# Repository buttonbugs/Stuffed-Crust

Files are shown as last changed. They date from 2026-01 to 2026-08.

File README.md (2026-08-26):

# Stuffed Crust



This repository contains the code for Wildcat Robotics' team Stuffed Crust. This is a fork of the open source melty brain code, openmelt [^1], with improved translational drift algorithm, adapted watchdog [^2] for [Teensy 4.0](https://www.pjrc.com/store/teensy40.html) and some other changes specific to Stuffed Crust's design.

## Preview

https://github.com/user-attachments/assets/2b465f3a-5d59-4c2d-9435-344acd4d646b

### References

[^1]: R. Olson and M. Schoppert, [“nothinglabs/openmelt2,”](https://github.com/nothinglabs/openmelt2/) July 2026. original-date: 2023-03-04T03:05:36Z.

[^2]: A. Brewer and S. Nobs, [“tonton81/WDT t4,”](https://github.com/tonton81/WDT_T4) Feb. 2026. original-date: 2020-01-
26T16:30:28Z.

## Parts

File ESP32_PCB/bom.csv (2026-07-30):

Qty | Comment | DNP | Exclude from BOM | Exclude from Board | Designator | Footprint | LCSC PN | Datasheet
3 | 1uF |  |  |  | C1,C2,C4 | Capacitor_SMD:C_0603_1608Metric | C15849 | ~
1 | 6.8uF |  |  |  | C3 | Capacitor_Tantalum_SMD:CP_EIA-3216-18_Kemet-A | C444749 | ~
1 | 10uF |  |  |  | C5 | Capacitor_Tantalum_SMD:CP_EIA-3216-18_Kemet-A | C7171 | ~
3 | 100nF |  |  |  | C6,C8,C13 | Capacitor_SMD:C_0603_1608Metric | C14663 | ~
1 | 10pF |  |  |  | C7 | Capacitor_SMD:C_0603_1608Metric | C106245 | ~
1 | 82pF |  |  |  | C9 | Capacitor_SMD:C_0603_1608Metric | C1683
1 | 47uF |  |  |  | C10 | Capacitor_SMD:C_0805_2012Metric | C16780
1 | 22uF |  |  |  | C11 | Capacitor_SMD:C_0603_1608Metric | C86295
1 | BAT54CW |  |  |  | D1 | Package_TO_SOT_SMD:SOT-323_SC-70 | C192144 | https://assets.nexperia.com/documents/data-sheet/BAT54W_SER.pdf
2 | SMAJ36A |  |  |  | D2,D3 | Diode_SMD:D_SMA | C148232 | https://www.littelfuse.com/media?itemid=75e32973-b177-4ee3-a0ff-cedaf1abdb93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
1 | Status_LED |  |  |  | D4 | LED_SMD:LED_0603_1608Metric | C19273151 | ~
1 | Power_LED |  |  |  | D5 | LED_SMD:LED_0603_1608Metric | C19171390 | ~
1 | USB_C_Receptacle |  |  |  | J1 | Connector_USB:USB_C_Receptacle_Molex_105450-0101 | C134092 | https://www.usb.org/sites/default/files/documents/usb_type-c.zip
1 | ESC 1 |  |  |  | J2 | ESC_Connectors:3_Pin |  | ~
1 | ESC 2 |  |  |  | J3 | ESC_Connectors:3_Pin |  | ~
1 | EN & Boot |  |  |  | J4 | Connector_PinHeader_2.54mm:PinHeader_2x04_P2.54mm_Vertical | C32713277 | ~
1 | LED_Strip |  |  |  | J5 | ESC_Connectors:LED_Strip |  | ~
1 | 10uH |  |  |  | L1 | Inductor_SMD:L_APV_APH0630 | C5349698 | ~
1 | 5.1K |  |  |  | R1 | Resistor_SMD:R_0603_1608Metric | C2907044 | ~
1 | 5.1k |  |  |  | R2 | Resistor_SMD:R_0603_1608Metric | C2907044 | ~
2 | 4.7k |  |  |  | R3,R4 | Resistor_SMD:R_0603_1608Metric | C99782 | ~
4 | 10k |  |  |  | R5,R6,R9,R12 | Resistor_SMD:R_0603_1608Metric | C98220 | ~
1 | 100k |  |  |  | R7 | Resistor_SMD:R_0805_2012Metric | C7319379 | ~
1 | 13.7 |  |  |  | R8 | Resistor_SMD:R_0805_2012Metric | C409962 | ~
2 | 100Ω |  |  |  | R10,R11 | Resistor_SMD:R_0603_1608Metric | C105588 | ~
1 | H3LIS331DL |  |  |  | U2 | accelerometer:TFLGA16_3X3X1_STM | C2655074 | https://www.st.com/resource/en/datasheet/h3lis331dl.pdf
1 | AP2112K-3.3 |  |  |  | U3 | Package_TO_SOT_SMD:SOT-23-5 | C23380830 | https://www.diodes.com/assets/Datasheets/AP2112.pdf
1 | TPS54302 |  |  |  | U4 | Package_TO_SOT_SMD:SOT-563 | C50310967 | http://www.ti.com/lit/ds/symlink/tps54302.pdf
1 | ESP32-S3-MINI-1U |  |  |  | U5 | RF_Module:ESP32-S2-MINI-1U | C2980299 | https://www.espressif.com/sites/default/files/documentation/esp32-s3-mini-1_mini-1u_datasheet_en.pdf

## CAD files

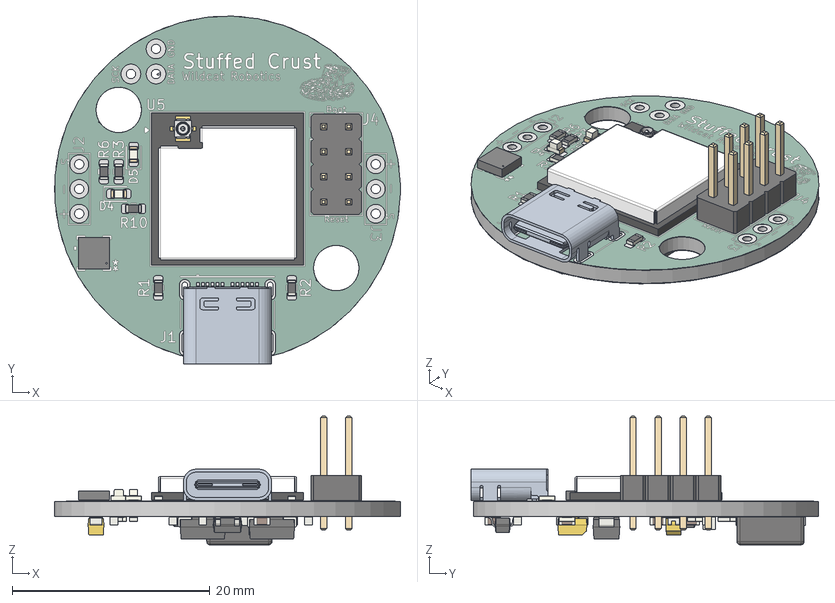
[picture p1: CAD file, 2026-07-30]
ESP32_PCB/ESP32_PCB.step
35.0 x 35.2 x 13.0 mm
R_0603_1608Metric x 10
LED_0603_1608Metric x 2
H3LIS331DLTR
PinHeader_2x04_P2.54mm_Vertical
uid__2482
C0402_20210301.xtd
C0201_20210301.xtd x 13
R0201_20210301.xtd x 3
ESP32-S3_20210301.xtd
ipx3.xtd
DFN1006.xtd
L0201_20210301.xtd x 2
XTAL3225_20210301.xtd
Imported
ESP32-S3-S2-MINI-solder_pad
ShieldBox_ESP32-S2-MINI-1U_V1.1_20231124
SOT-323_SC-70
D_SMA x 2
C_0603_1608Metric x 9
R_0805_2012Metric x 2
C_0805_2012Metric
CP_EIA-3216-18_Kemet-A x 2
L_APV_APH0630
TSOT-23-6
SOT-23-5
ESP32_PCB_copper
ESP32_PCB_pad
ESP32_PCB_via
ESP32_PCB_silkscreen x 2
ESP32_PCB_soldermask x 2
ESP32_PCB_PCB

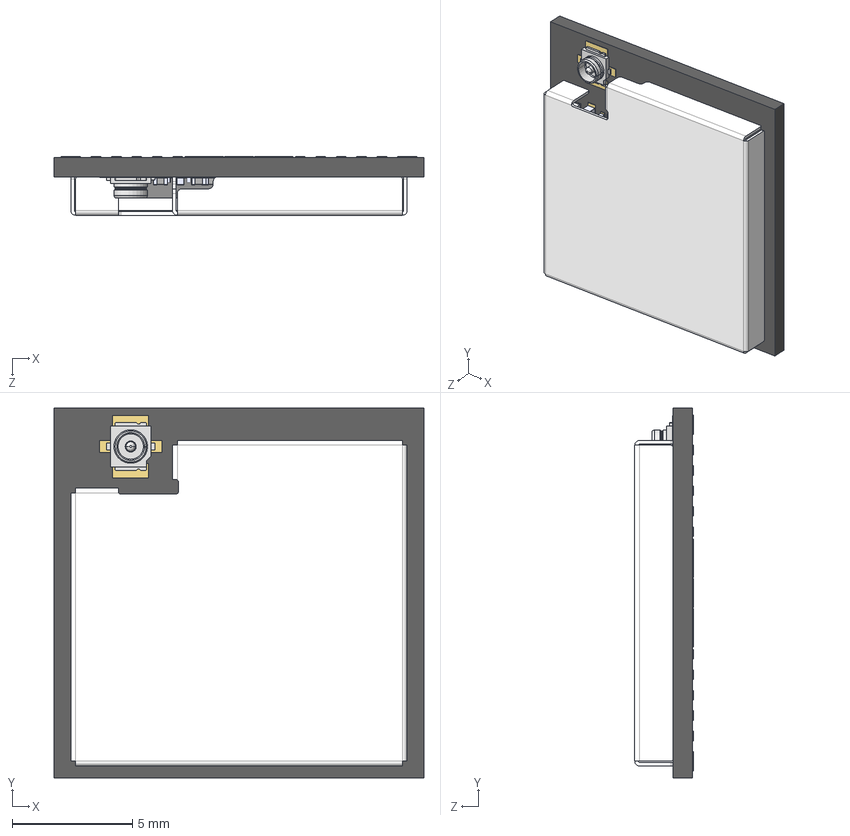
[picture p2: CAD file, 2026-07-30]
ESP32_PCB/imports/ESP32-S3-MINI-1U/ESP32-S3-MINI-1U.STEP
15.4 x 15.4 x 2.44 mm
uid__2482
C0402_20210301.xtd
C0201_20210301.xtd x 13
R0201_20210301.xtd x 3
ESP32-S3_20210301.xtd
ipx3.xtd
DFN1006.xtd
L0201_20210301.xtd x 2
XTAL3225_20210301.xtd
Imported
ESP32-S3-S2-MINI-solder_pad
ShieldBox_ESP32-S2-MINI-1U_V1.1_20231124

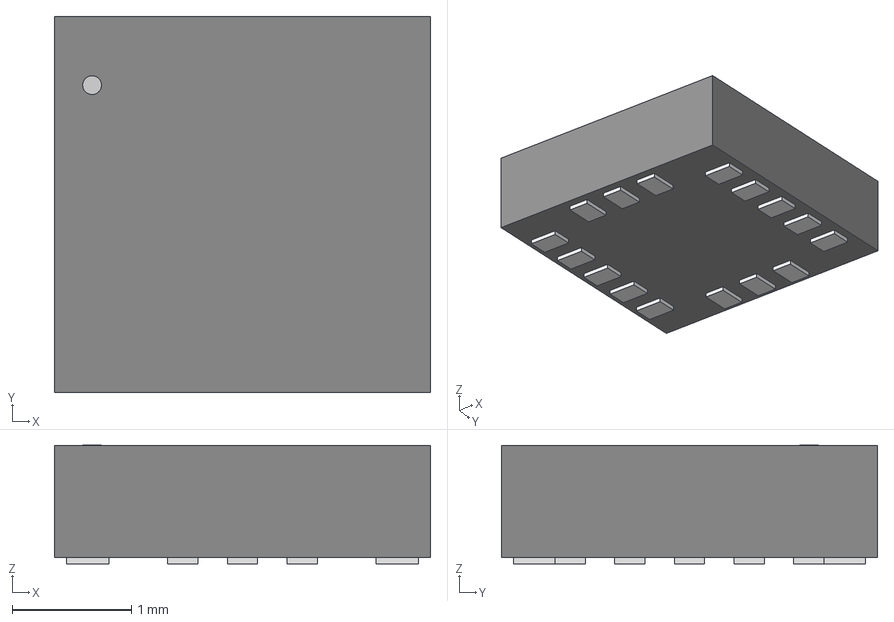
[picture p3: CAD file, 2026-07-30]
ESP32_PCB/imports/ul_H3LIS331DL/H3LIS331DLTR.step
3.15 x 3.15 x 0.993 mm

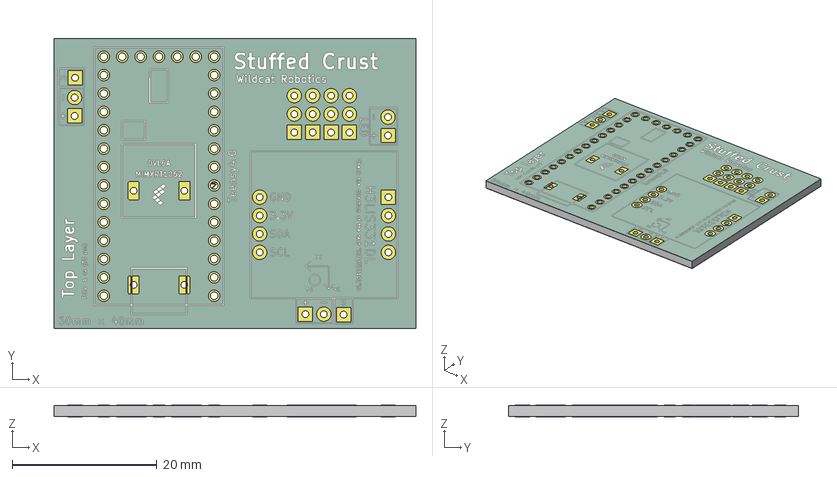
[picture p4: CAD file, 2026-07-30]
PCB/3D_models/PCB_v1.step
50.0 x 40.0 x 1.66 mm
PCB_v1_copper
PCB_v1_silkscreen x 2
PCB_v1_soldermask x 2
PCB_v1_PCB

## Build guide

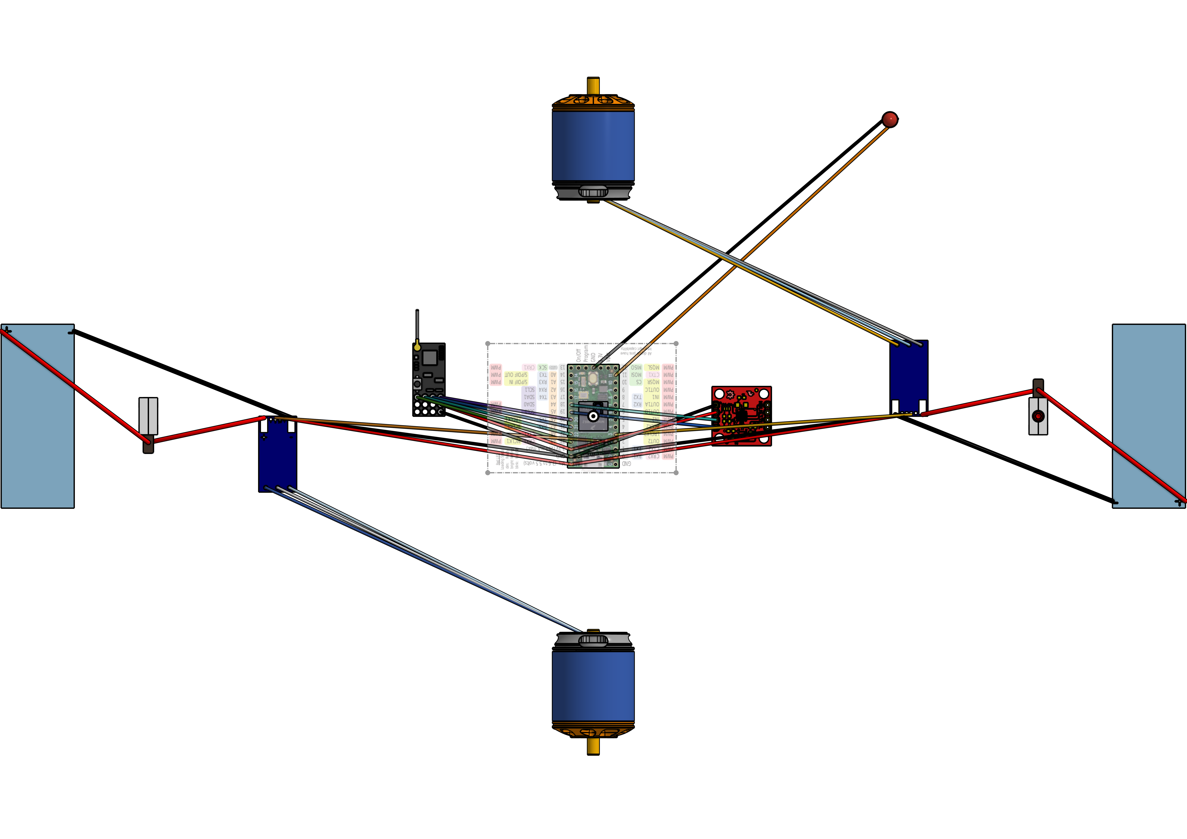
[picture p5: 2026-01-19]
Wiring.png

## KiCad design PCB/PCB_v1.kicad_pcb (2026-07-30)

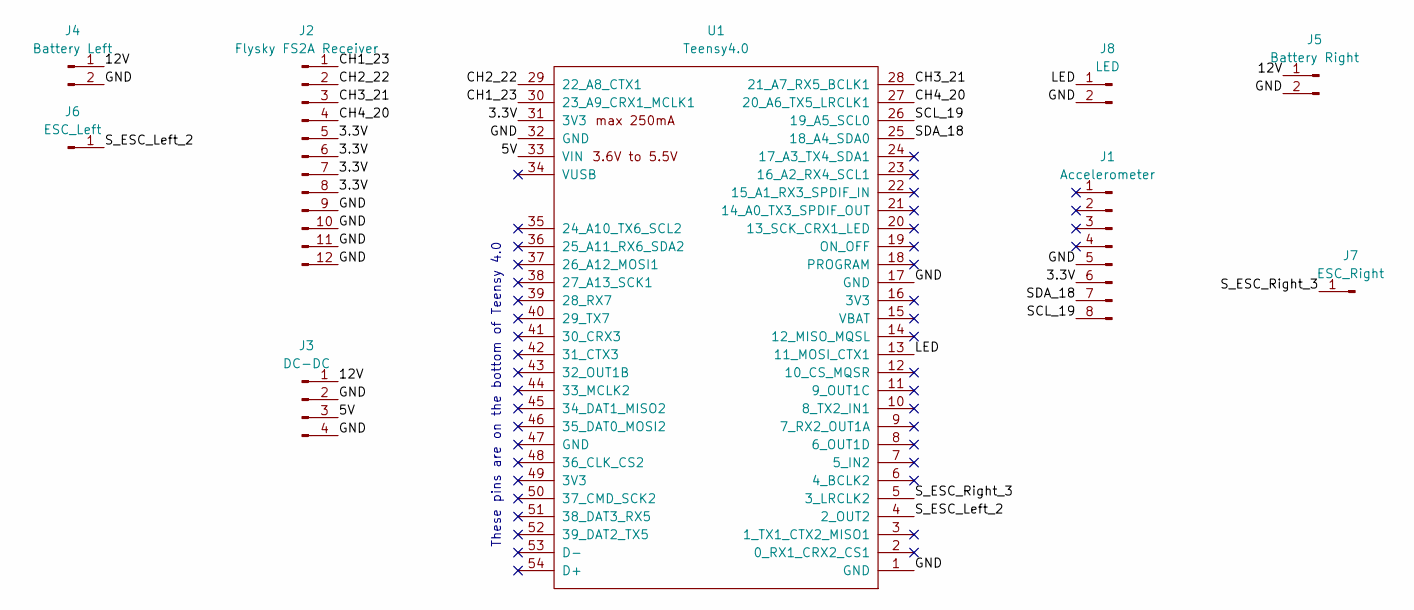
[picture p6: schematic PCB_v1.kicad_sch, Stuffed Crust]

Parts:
J1: Accelerometer
J2: Flysky FS2A Receiver; Flysky_FS2A_Receiver
J3: DC-DC; DC_DC
J4: Battery Left; Battery
J5: Battery Right; Battery
J6: ESC_Left; ESC
J7: ESC_Right; ESC
J8: LED
U1: Teensy4.0; Teensy40

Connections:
/3.3V: J1.6, J2.5, J2.6, J2.7, J2.8, U1.31 (3V3)
/5V: J3.3, U1.33 (VIN)
/12V: J3.1, J4.1, J5.1
/CH1_23: J2.1, U1.30 (23_A9_CRX1_MCLK1)
/CH2_22: J2.2, U1.29 (22_A8_CTX1)
/CH3_21: J2.3, U1.28 (21_A7_RX5_BCLK1)
/CH4_20: J2.4, U1.27 (20_A6_TX5_LRCLK1)
/GND: J1.5, J2.9, J2.10, J2.11, J2.12, J3.2, J3.4, J4.2, J5.2, J8.2, U1.1 (GND), U1.17 (GND), U1.32 (GND)
/LED: J8.1, U1.13 (11_MOSI_CTX1)
/SCL_19: J1.8, U1.26 (19_A5_SCL0)
/SDA_18: J1.7, U1.25 (18_A4_SDA0)
/S_ESC_Left_2: J6.1, U1.4 (2_OUT2)
/S_ESC_Right_3: J7.1, U1.5 (3_LRCLK2)

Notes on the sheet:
These pins are on the bottom of Teensy 4.0

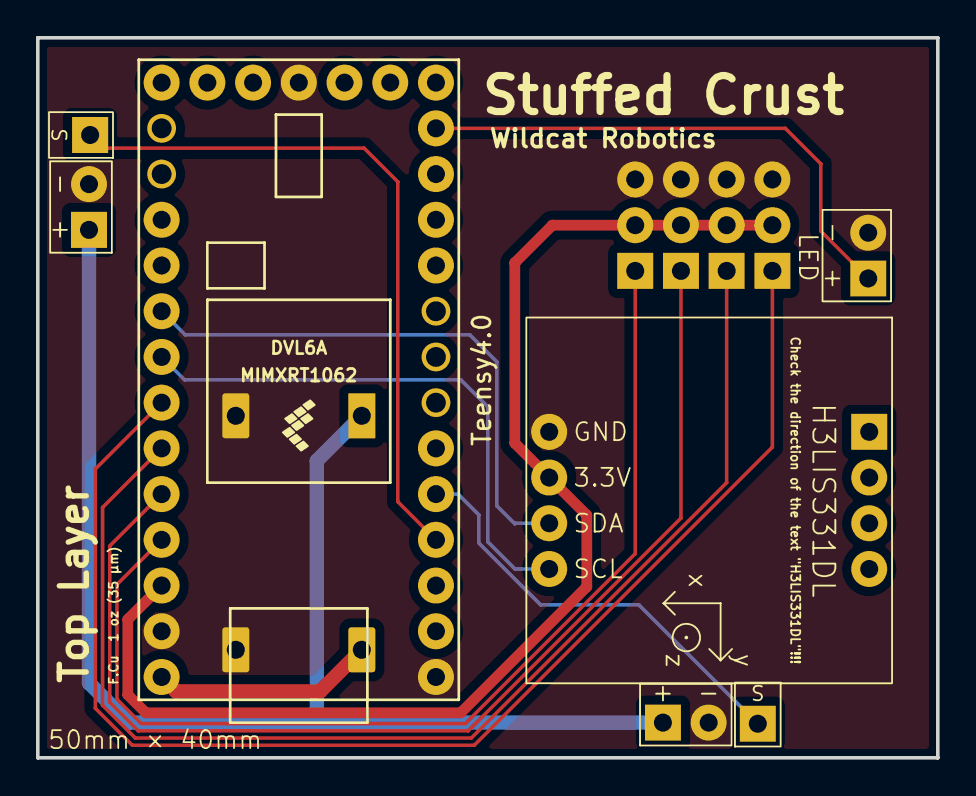
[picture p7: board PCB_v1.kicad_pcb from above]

Board: 2 copper layers, 50.0 x 40.0 mm, 9 parts (0 on the bottom side), 13 nets.

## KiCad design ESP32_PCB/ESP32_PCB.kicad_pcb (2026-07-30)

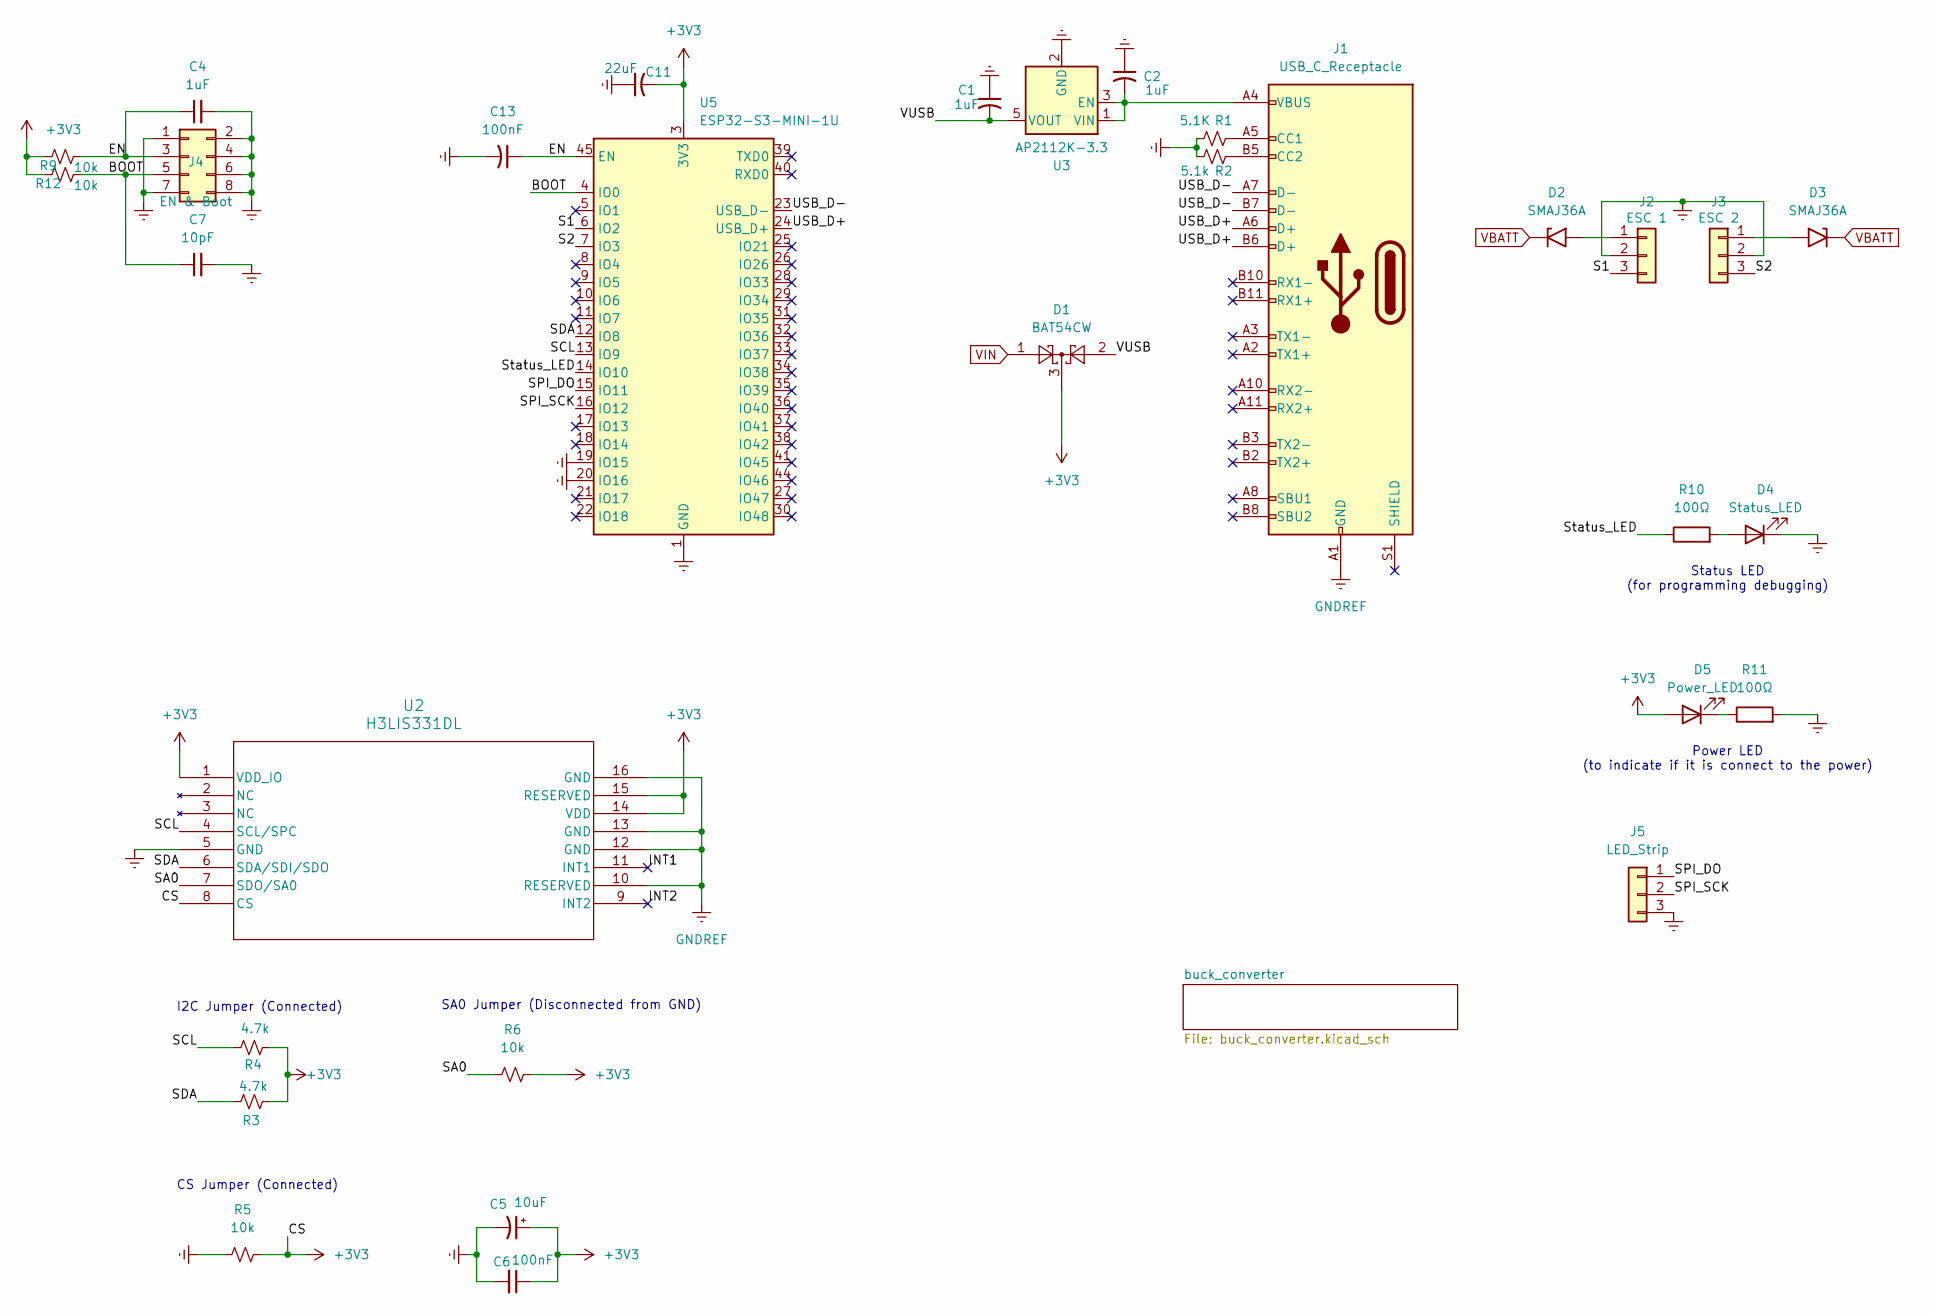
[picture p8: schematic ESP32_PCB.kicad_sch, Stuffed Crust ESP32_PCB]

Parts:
C1, C2, C4: 1uF; C_0603_1608Metric; LCSC PN C15849
C5: 10uF; CP_EIA-3216-18_Kemet-A; LCSC PN C7171
C6, C13: 100nF; C_0603_1608Metric; LCSC PN C14663
C7: 10pF; C_0603_1608Metric; LCSC PN C106245
C11: 22uF; C_0603_1608Metric; LCSC PN C86295
D1: BAT54CW; SOT-323_SC-70; LCSC PN C192144
D2, D3: SMAJ36A; D_SMA; LCSC PN C148232
D4: Status_LED; LED_0603_1608Metric; LCSC PN C19273151
D5: Power_LED; LED_0603_1608Metric; LCSC PN C19171390
J1: USB_C_Receptacle; USB_C_Receptacle_Molex_105450-0101; LCSC PN C134092
J2: ESC 1; 3_Pin
J3: ESC 2; 3_Pin
J4: EN & Boot; PinHeader_2x04_P2.54mm_Vertical; LCSC PN C32713277
J5: LED_Strip
R1: 5.1K; R_0603_1608Metric; LCSC PN C2907044
R2: 5.1k; R_0603_1608Metric; LCSC PN C2907044
R3, R4: 4.7k; R_0603_1608Metric; LCSC PN C99782
R5, R6, R9, R12: 10k; R_0603_1608Metric; LCSC PN C98220
R10, R11: 100Ω; R_0603_1608Metric; LCSC PN C105588
U2: H3LIS331DL; TFLGA16_3X3X1_STM; LCSC PN C2655074
U3: AP2112K-3.3; SOT-23-5; LCSC PN C23380830
U5: ESP32-S3-MINI-1U; ESP32-S2-MINI-1U; LCSC PN C2980299

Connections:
+3V3: C5.1, C6.1, C11.2, D1.3, D5.2 (A), R3.1, R4.1, R5.2, R6.2, R9.2, R12.2, U2.1 (VDD_IO), U2.8 (CS), U2.14 (VDD), U2.15 (RESERVED), U5.3 (3V3)
/BOOT: C7.1, J4.5, R12.1, U5.4 (IO0)
/EN: C4.1, C13.1, J4.3, R9.1, U5.45 (EN)
/INT1: U2.11 (INT1)
/INT2: U2.9 (INT2)
/S1: J2.3, U5.6 (IO2)
/S2: J3.3, U5.7 (IO3)
/SA0: R6.1, U2.7 (SDO/SA0)
/SCL: R4.2, U2.4 (SCL/SPC), U5.13 (IO9)
/SDA: R3.2, U2.6 (SDA/SDI/SDO), U5.12 (IO8)
/SPI_DO: J5.1, U5.15 (IO11)
/SPI_SCK: J5.2, U5.16 (IO12)
/Status_LED: R10.1, U5.14 (IO10)
/USB_D+: J1.A6 (D+), J1.B6 (D+), U5.24 (USB_D+)
/USB_D-: J1.A7 (D-), J1.B7 (D-), U5.23 (USB_D-)
/VUSB: C1.2, D1.2, U3.5 (VOUT)
GNDREF: C1.1, C2.1, C4.2, C5.2, C6.2, C7.2, C11.1, C13.2, D4.1 (K), J1.A1 (GND), J1.A12 (GND), J1.B1 (GND), J1.B12 (GND), J2.2, J3.2, J4.1, J4.2, J4.4, J4.6, J4.7, J4.8, J5.3, R1.1, R2.1, R5.1, R11.2, U2.5 (GND), U2.10 (RESERVED), U2.12 (GND), U2.13 (GND), U2.16 (GND), U3.2 (GND), U5.1 (GND), U5.2 (GND), U5.19 (IO15), U5.20 (IO16), U5.42 (GND), U5.43 (GND), U5.46 (GND), U5.47 (GND), U5.48 (GND), U5.49 (GND), U5.50 (GND), U5.51 (GND), U5.52 (GND), U5.53 (GND), U5.54 (GND), U5.55 (GND), U5.56 (GND), U5.57 (GND), U5.58 (GND), U5.59 (GND), U5.60 (GND), U5.61 (GND), U5.62 (GND), U5.63 (GND), U5.64 (GND), U5.65 (GND); also elsewhere on the board
unnamed: D2.2 (A2), J2.1
unnamed: D3.2 (A2), J3.1
unnamed: D4.2 (A), R10.2
unnamed: D5.1 (K), R11.1
unnamed: J1.A5 (CC1), R1.2
unnamed: J1.B5 (CC2), R2.2
unnamed: C2.2, J1.A4 (VBUS), J1.A9 (VBUS), J1.B4 (VBUS), J1.B9 (VBUS), U3.1 (VIN), U3.3 (EN)
VBATT: D2.1 (A1), D3.1 (A1); also elsewhere on the board
VIN: D1.1; also elsewhere on the board

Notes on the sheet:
Power LED (to indicate if it is connect to the power)
Status LED (for programming debugging)
CS Jumper (Connected)
I2C Jumper (Connected)
SA0 Jumper (Disconnected from GND)

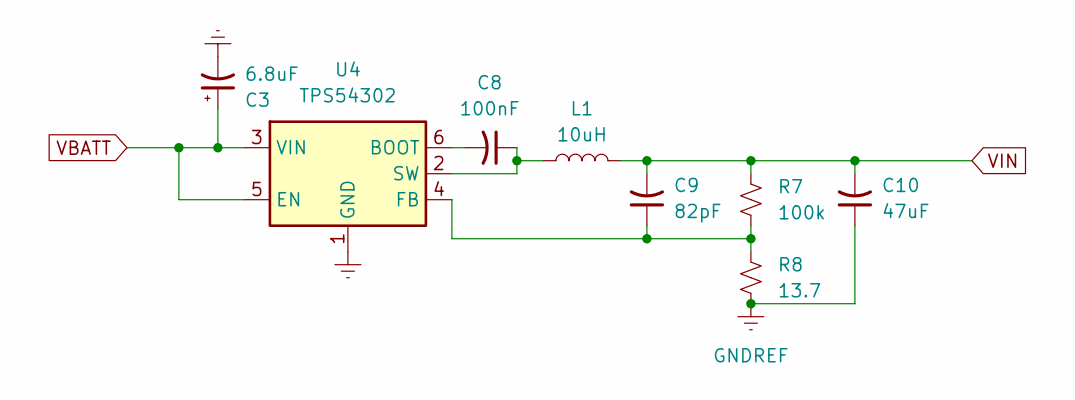
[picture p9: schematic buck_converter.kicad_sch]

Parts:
C3: 6.8uF; CP_EIA-3216-18_Kemet-A; LCSC PN C444749
C8: 100nF; C_0603_1608Metric; LCSC PN C14663
C9: 82pF; C_0603_1608Metric; LCSC PN C1683
C10: 47uF; C_0805_2012Metric; LCSC PN C16780
L1: 10uH; L_APV_APH0630; LCSC PN C5349698
R7: 100k; R_0805_2012Metric; LCSC PN C7319379
R8: 13.7; R_0805_2012Metric; LCSC PN C409962
U4: TPS54302; TSOT-23-6; LCSC PN C311983

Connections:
GNDREF: C3.2, C10.1, R8.2, U4.1 (GND); also elsewhere on the board
unnamed: C8.2, U4.6 (BOOT)
unnamed: C9.1, R7.2, R8.1, U4.4 (FB)
unnamed: C8.1, L1.1, U4.2 (SW)
VBATT: C3.1, U4.3 (VIN), U4.5 (EN); also elsewhere on the board
VIN: C9.2, C10.2, L1.2, R7.1; also elsewhere on the board

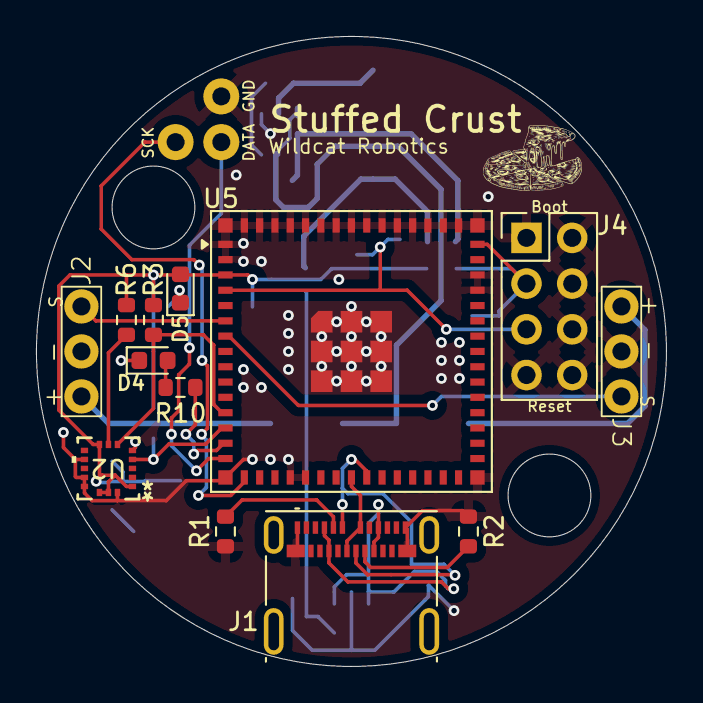
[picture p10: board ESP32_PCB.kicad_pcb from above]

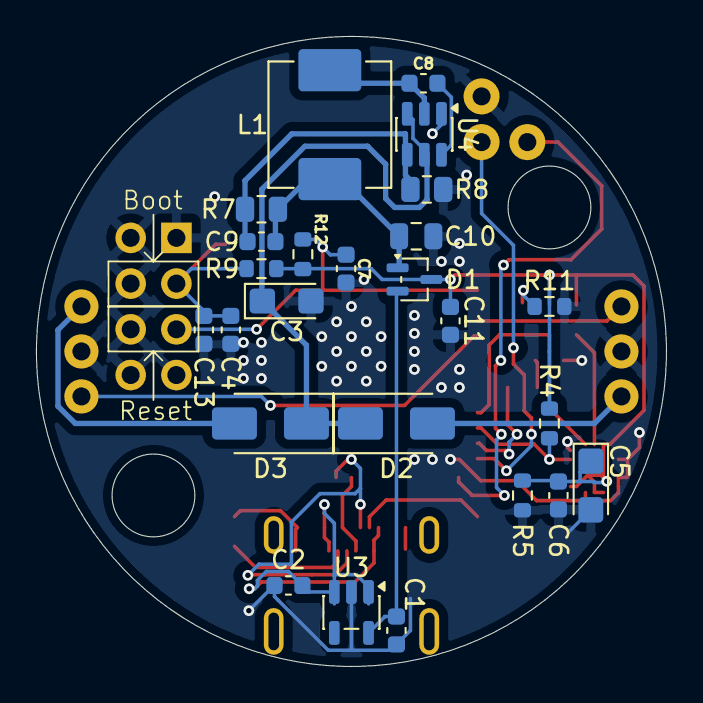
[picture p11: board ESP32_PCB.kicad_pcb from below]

Board: 2 copper layers, 35.0 x 35.0 mm, 39 parts (25 on the bottom side), 27 nets.

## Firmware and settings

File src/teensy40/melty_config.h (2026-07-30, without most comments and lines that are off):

#define MELTY_CONFIG_GUARD
#define ENABLE_EEPROM_STORAGE                     //Comment out this to disable EEPROM (for ARM)
#define EEPROM_WRITTEN_SENTINEL_VALUE 42          //Changing this value will cause existing EEPROM values to be invalidated (revert to defaults)
#define DEFAULT_ACCEL_MOUNT_RADIUS_CM 2.45         //Radius of accelerometer from center of robot
#define DEFAULT_LED_OFFSET_PERCENT 13              //Adjust to make heading LED line up with direction robot travels 0-99 (increasing moves beacon clockwise)
#define DEFAULT_ACCEL_ZERO_G_OFFSET_Z 2.7f
#define DEFAULT_ACCEL_ZERO_G_OFFSET_X 0.0f          //Value accelerometer returns with robot at rest (in G) - adjusts for any offset
#define LEFT_RIGHT_HEADING_CONTROL_DIVISOR 1.5f   //How quick steering is (larger values = slower)
#define MIN_TRANSLATION_RPM 400                   //full power spin in below this number (increasing can reduce spin-up time)
#define ENABLE_REVERSE                              //Enable motor reverse
#define LOW_SPEED_FORBACK_THROTTLE_PERCENT 0.5f
#define LOW_SPEED_REVOLUTION_THROTTLE_PERCENT 0.4f
#define LEFTRIGHT_RC_CHANNEL_PIN 20                //To Left / Right on RC receiver
#define FORBACK_RC_CHANNEL_PIN 21                  //To Forward / Back on RC receiver (Pin 1 on Arduino Micro labelled as "TX" - https://docs.arduino.cc/hacking/hardware/PinMapping32u4)
#define THROTTLE_RC_CHANNEL_PIN 22                 //To Throttle on RC receiver (Pin 0 on Arduino Micro labelled as "RX" - https://docs.arduino.cc/hacking/hardware/PinMapping32u4)
#define REVOLUTION_RC_CHANNEL_PIN 23                  //To Heading / Spin direction on RC receiver (Pin 4 on Arduino Micro - https://docs.arduino.cc/hacking/hardware/PinMapping32u4)
#define HEADING_LED_1_PIN 11                         //To heading LED (pin 13 is on-board Arduino LED)
#define HEADING_LED_2_PIN 12                         //
#define LED_STRIP_DATA 11                           // LED strip SPI DO/MOSI pin
#define LED_STRIP_SCK 12                            // LED strip SPI SCK/Clock pin
#define MOTOR_PIN1 2                              //Pin for Motor 1 driver
#define MOTOR_PIN2 3                             //Pin for Motor 2 driver
#define BATTERY_ADC_PIN A0                        //Pin for battery monitor (if enabled)
enum throttle_modes {
    BINARY_THROTTLE,    //Motors pins are fully on/off - throttle controlled by portion of each rotation motor is on (no PWM)
    FIXED_PWM_THROTTLE, //Motors pins are PWM at PWM_MOTOR_ON, PWM_MOTOR_COAST or PWM_MOTOR_OFF
    DYNAMIC_PWM_THROTTLE//Scales PWM throttling between PWM_MOTOR_COAST and PWM_MOTOR_ON
};
#define THROTTLE_TYPE DYNAMIC_PWM_THROTTLE      //<---Throttle type set here!
#define DYNAMIC_PWM_MOTOR_ON_PORTION 0.5f       //if defined (and DYNAMIC_PWM_THROTTLE is set) portion of each rotation motor is on is fixed at this value
#define DYNAMIC_PWM_THROTTLE_PERCENT_MAX 1.0f   //Range of RC throttle DYNAMIC_PWM_THROTTLE is applied to
#define LOW_SPEED_RC_THROTTLE_THRESHOLD 15       //0 - 100; turn on low_speed_mode if rc_get_throttle_percent() < LOW_SPEED_RC_THROTTLE_THRESHOLD
#define PWM_MOTOR_ON 230                          //Motor PWM ON duty cycle (Simonk: 140 seems barely on / 230 seems a good near-full-throttle value)
#define PWM_MOTOR_COAST 100                       //Motor PWM COAST duty cycle - set to same as PWM_ESC_MOTOR_OFF for fully unpowered (best translation?)
#define PWM_MOTOR_OFF 100                         //Motor PWM OFF duty cycle (Simonk: 100 worked well in testing - if this is too low - ESC may not init)
#define BATTERY_ALERT_ENABLED                     //if enabled - heading LED will flicker when battery voltage is low
#define VOLTAGE_DIVIDER 11                        //(~10:1 works well - 10kohm to GND, 100kohm to Bat+).  Resistors have tolerances!  Adjust as needed...
#define BATTERY_ADC_WARN_VOLTAGE_THRESHOLD 7.0f  //If voltage drops below this value - then alert is triggered
#define ARDUINIO_VOLTAGE 5.0f                     //Needed for ADC maths for battery monitor
#define LOW_BAT_REPEAT_READS_BEFORE_ALARM 20      //Requires this many ADC reads below threshold before alarming
#define ENABLE_WATCHDOG                           //Uses WDT_T4's watchdog to enable watchdog / reset (tested on AVR - should work for ARM https://github.com/tonton81/WDT_T4)
#define WATCH_DOG_TIMEOUT_MS 10000                 //Timeout value for watchdog (not all values are supported - 2000ms verified with Arudino Micro)
#define VERIFY_RC_THROTTLE_ZERO_AT_BOOT           //Requires RC throttle be 0% at boot to allow spin-up for duration of MAX_MS_BETWEEN_RC_UPDATES (about 1 second)
#define ENABLE_ESP32_SPIN_CONTROL                 // Using esp32_spin_control.h to handle high speed mode

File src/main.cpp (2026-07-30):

// See melty_config.h for configuration parameters

#include <Arduino.h>
#include "rc_handler.h"
#include "melty_config.h"
#include "motor_driver.h"
#include "accel_handler.h"
#include "spin_control.h"
#include "motor_low_speed.h"
#include "config_storage.h"
#include "led_driver.h"
#include "battery_monitor.h"

#ifndef BOARD_TEENSY40
    #include "data_relay.h"
#endif

// loops until a good RC signal is detected and throttle is zero (assures safe start)
static void wait_for_rc_good_and_zero_throttle() {
    while (rc_signal_is_healthy() == false || rc_get_throttle_percent() > 0) {
        //"slow on/off" for LED while waiting for signal
        heading_led_on(0);
        delay(250);
        heading_led_off();
        delay(250);

        // services watchdog and echo diagnostics while we are waiting for RC signal
        service_watchdog();
    }
}

// INITIAL SETUP
void setup() {
    Serial.begin(115200);

    // get motor drivers setup (and off!) first thing
    init_motors();
    init_led();

    // returns actual watchdog timeout MS
    init_watchdog();

    init_rc();
    init_accel();  // accelerometer uses i2c - which can fail blocking (so only initializing it -after- the watchdog is running)
    #ifndef BOARD_TEENSY40
        start_accel_task();  // start accelerometer task immediately after init
    #endif

#ifdef DATA_RELAY
    init_relay();
#endif

// load settings on boot
#ifdef ENABLE_EEPROM_STORAGE
    load_melty_config_settings();
#endif

// if JUST_DO_DIAGNOSTIC_LOOP - then we just loop and display debug info via USB (good for testing)
#ifdef JUST_DO_DIAGNOSTIC_LOOP
    while (1) {
        service_watchdog();
        echo_diagnostics();
        delay(250);  // delay prevents serial from getting flooded (can cause issues programming)
    }
#endif

#ifdef VERIFY_RC_THROTTLE_ZERO_AT_BOOT
    wait_for_rc_good_and_zero_throttle();  // Wait for good RC signal at zero throttle
    delay(MAX_MS_BETWEEN_RC_UPDATES + 1);  // Wait for first RC signal to have expired
    wait_for_rc_good_and_zero_throttle();  // Verify RC signal is still good / zero throttle
#endif
}

// dumps out diagnostics info
static void echo_diagnostics() {
    Serial.print("Raw Accel G: ");
    Serial.print(get_accel_force_g());
    
    Serial.print("  RC Health: ");
    Serial.print(rc_signal_is_healthy());
    
    Serial.print("  RC Throttle: ");
    Serial.print(rc_get_throttle_percent());
    
    Serial.print("  RC L/R: ");
    Serial.print(rc_get_leftright());
    
    Serial.print("  RC F/B: ");
    Serial.print(rc_get_forback());

#ifdef BATTERY_ALERT_ENABLED
    Serial.print("  Battery Voltage: ");
    Serial.print(get_battery_voltage());
#endif

#ifdef ENABLE_EEPROM_STORAGE
    Serial.print("  Accel Radius: ");
    Serial.print(load_accel_mount_radius());

    Serial.print("  Heading Offset: ");
    Serial.print(load_heading_led_offset());

    Serial.print("  Zero G Offset: ");
    Serial.print(load_accel_zero_g_offset());

    Serial.print("Gyro Z: ");
    Serial.print(gyro_z);
    
#endif
    Serial.println("");
}

// Used to flash out max recorded RPM 100's of RPMs
static void display_rpm_if_requested() {
    // #ifdef BOARD_TEENSY40
    // // triggered by user pushing throttle up while bot is at idle for 750ms
    // if (rc_get_forback() == RC_FORBACK_FORWARD) {
    //     delay(750);
    //     // verify throttle at zero to prevent accidental entry into RPM flash
    //     if (rc_get_forback() == RC_FORBACK_FORWARD && rc_get_throttle_percent() == 0) {
    //         // throttle up cancels RPM count
    //         for (int x = 0; x < get_max_rpm() && rc_get_throttle_percent() == 0; x = x + 100) {
    //             service_watchdog();  // flashing out RPM can take a while - need to assure watchdog doesn't trigger
    //             delay(600);
    //             heading_led_on(0);
    //             delay(20);
    //             heading_led_off();
    //         }
    //         delay(1500);  // flash-out punctuated with delay to make clear RPM count has completed
    //     }
    // }
    // #endif
}

// checks if user has requested to enter / exit config mode
static void check_config_mode() {
    // #ifdef BOARD_TEENSY40
    // // if user pulls control stick back for 150ms - enters (or exits) interactive configuration mode
    // if (rc_get_forback() == RC_FORBACK_BACKWARD) {
    //     delay(150);
    //     if (rc_get_forback() == RC_FORBACK_BACKWARD) {
    //         toggle_config_mode();
    //         if (get_config_mode() == false)
    //             save_melty_config_settings();  // save melty settings on config mode exit

    //         // wait for user to release stick - so we don't re-toggle modes
    //         while (rc_get_forback() == RC_FORBACK_BACKWARD) {
    //             service_watchdog();
    //         }
    //     }
    // }
    // #endif
}

// handles the bot when not spinning (with RC good)
static void handle_bot_idle() {
    motors_off();  // assure motors are off

    // normal LED "fast flash" - indicates RC signal is good while sitting idle
    heading_led_on(0);
    delay(30);
    heading_led_off();
    delay(120);

    // if in config mode blip LED again to show "double-flash"
    // if (get_config_mode() == true) {
    //     heading_led_off();
    //     delay(400);
    //     heading_led_on(0);
    //     delay(30);
    //     heading_led_off();
    //     delay(140);
    // }

    check_config_mode();         // check if user requests we enter / exit config mode
    display_rpm_if_requested();  // flashed out RPM if user has requested

    echo_diagnostics();  // echo diagnostics if bot is idle
}

// main control loop
void loop() {
    service_watchdog();  // keep the watchdog happy

    service_rc();
    #ifdef DATA_RELAY
        if(config_mode){
        #ifdef BOARD_TEENSY40
        relay_data({
            (uint8_t)rc_get_throttle_percent(), 
            (uint8_t)get_battery_voltage(), 
            (uint8_t)(get_accel_force_g()),  // convert to 0-100 scale (with 1 decimal place)
            0,0,0
        });
        #else
        relay_data({
            (uint8_t)rc_get_throttle_percent(), 
            (uint8_t)get_battery_voltage(),
            0,
            (uint8_t)(get_accel_force_g()),  // convert to 0-100 scale (with 1 decimal place)
            0,(uint16_t)(current_frequency * 60.0f),
            (float)accel_mount_radius_cm,
            (uint32_t)interval_micros,
            (int)(led_offset_ratio * 100.0f)
        });
        #endif
        } else {
            Serial.print("Interval: ");
            Serial.println(interval_micros);

            Serial.print("Current Frequency (RPS): ");
            Serial.println(current_frequency);

            Serial.print("Current LED Offset (%): ");
            Serial.println(led_offset_ratio * 100);
        }
    #endif

    // if the rc signal isn't good - assure motors off - and "slow flash" LED
    // this will interrupt a spun-up bot if the signal becomes bad
    while (rc_signal_is_healthy() == false) {
        motors_off();

        heading_led_on(0);
        delay(30);
        heading_led_off();
        delay(600);

        // services watchdog and echo diagnostics while we are waiting for RC signal
        service_watchdog();
        echo_diagnostics();
    }

    // if RC is good - and throtte is above 0 - spin a single rotation
    if (rc_get_throttle_percent() > LOW_SPEED_RC_THROTTLE_THRESHOLD) {
        #ifdef ENABLE_ESP32_SPIN_CONTROL
            high_speed_set_motor();
        #else
            // this is where all the motor control happens!  (see spin_control.cpp)
            spin_one_rotation();
        #endif
    } else {
        #ifdef BOARD_TEENSY40
            if (rc_get_throttle_percent() < 5) {
                handle_bot_idle();
            }
        #else
            bool current_led_status = (millis() % 150 < 30);
            digitalWrite(HEADING_LED_1_PIN, current_led_status);     // Blink the LED the same way as handle_bot_idle() without using delay()
            digitalWrite(HEADING_LED_2_PIN, current_led_status);     // Blink the LED the same way as handle_bot_idle() without using delay()
        #endif

        low_speed_set_motor();
    }
}

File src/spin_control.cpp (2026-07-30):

#include <Arduino.h>
#include "spin_control.h"

#include "rc_handler.h"
#include "led_driver.h"
#include "accel_handler.h"
#include "motor_driver.h"

#include "melty_config.h"
#include "config_storage.h"

/* 
    Purpose of this file:
        NOT TO use any "delay()" or "while loop for the whole revolution" in high_speed_set_motor()

    Usage:
        put high_speed_set_motor() inside the loop() in main.cpp
 */

#define GRAVITATIONAL_ACCELERATION 9.8f      // m / s^2
#define MOTOR_COAST_THROTTLE 0.05f
#define MAX_HEADING_LED_REVOLUTION_SPEED 1.4f   // revolutions per second, maximum heading LED revolution speed

uint32_t last_measurement_micros = 0;       // microseconds, the value of micros() when setting the last last_measurement_frequency
uint32_t interval_micros = 0;               // microseconds, interval of running update_robot_direction()
float last_measurement_frequency = 0.0f;    // Hz (or revolutions per second) of the spin
float robot_direction = 0.0f;
float current_frequency = 1.0f;

float accel_mount_radius_cm = DEFAULT_ACCEL_MOUNT_RADIUS_CM;
static float accel_zero_g_offset = DEFAULT_ACCEL_ZERO_G_OFFSET_X;

// loads settings from EEPROM
void load_melty_config_settings_esp32() {       // Avoid multiple definition of `load_melty_config_settings()`
#ifdef ENABLE_EEPROM_STORAGE
    accel_mount_radius_cm = load_accel_mount_radius();
    accel_zero_g_offset = load_accel_zero_g_offset();
#endif
}

void load_melty_config_settings() {
    load_melty_config_settings_esp32();
    last_measurement_micros = micros();  // uint32_t overflows in 70 minutes.
}

// Config Mode
void update_config() {
    #ifndef BOARD_TEENSY40
        if (config_left) {
            accel_mount_radius_cm -= 0.00002f;
        } else if (config_right) {
            accel_mount_radius_cm += 0.00002f;
        }
        if (config_heading) {
            led_offset_ratio += 0.0004f;
            led_offset_ratio -= floor(led_offset_ratio);    // Restrict led_offset_ratio in [0.0, 1.0)
        }
    #endif
}

// This function changes the direction of the heading LED
// interval: seconds that have passed since last call of this function
void rotational_motion(float interval) {
    if (config_mode) {
        /* config mode */
    } else {
        robot_direction += MAX_HEADING_LED_REVOLUTION_SPEED * revolution_ratio * interval;
    }
}

void translational_motion() {
    float motor_1_throttle = 1.0f;          // ranging from -1.0 to 1.0
    float motor_2_throttle = 1.0f;          // ranging from -1.0 to 1.0
    float translation_throttle = constrain(sqrt(sq(forback_ratio) + sq(leftright_ratio)), -1.0f, 1.0f); // the throttle of the translation joystick
    float translation_direction;            // the direction of the translation joystick, using +y-axis as the 0 direction

    // Calculation translation direction, return from 0.0 to 1.0
    if (leftright_ratio == 0.0f) {
        if (forback_ratio > 0.0f) {
            translation_direction = 0.0f;
        } else {
            translation_direction = 0.5f;
        }
    } else {
        translation_direction = atan2(forback_ratio, leftright_ratio) / (2.0f * PI);   // Use +x-axis as the 0 direction
        translation_direction -= 0.25f;     // Use +y-axis as the 0 direction
    }

    /* Check if the robot rotates to the translation direction */
    float direction_difference = robot_direction - translation_direction;
    /* 
    modulo direction_difference to [-0.5, 0.5)
    For example:
    1.6 -> -0.4
    1.4 -> +0.4
    0.9 -> -0.1
    0.4 -> +0.4
    -0.6 -> +0.4
    -1.2 -> -0.2
    -1.4 -> -0.4
    -1.6 -> +0.4
    */
    direction_difference -= floor(direction_difference + 0.5f);
    
    // take abosulte value
    direction_difference = abs(direction_difference);   // return [0.0, 0.5]

    // Set motor throttle
    if (direction_difference < 0.25f * translation_throttle) {
        // Assuming motor 1 is on the left, motor 2 is on the right
        motor_1_throttle = MOTOR_COAST_THROTTLE;
        motor_2_throttle = 2.0f * motor_2_throttle - MOTOR_COAST_THROTTLE;  // For symmetry, making robot more stable
    } else if (0.5f - direction_difference < 0.25f * translation_throttle) {
        // Assuming motor 1 is on the left, motor 2 is on the right
        motor_2_throttle = MOTOR_COAST_THROTTLE;
        motor_1_throttle = 2.0f * motor_1_throttle - MOTOR_COAST_THROTTLE;  // For symmetry, making robot more stable
    }
    
    motor_1_throttle *= throttle_ratio;
    motor_2_throttle *= throttle_ratio;
    motor_1_throttle = constrain(motor_1_throttle, -1.0f, 1.0f);
    motor_2_throttle = constrain(motor_2_throttle, -1.0f, 1.0f);
    motor_1_on(motor_1_throttle);
    motor_2_on(motor_2_throttle);
}
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

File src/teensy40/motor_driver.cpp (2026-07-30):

#include <Arduino.h>
#include <Servo.h>
#include "melty_config.h"
#include "motor_driver.h"
#include "map_float.h"

Servo motor1;
Servo motor2;

constexpr uint16_t ESC_MIN_US   = 1000;
constexpr uint16_t ESC_MAX_US   = 2000;
constexpr uint16_t ESC_STOP_US  = 1500;
constexpr uint16_t ESC_COAST_DIFF_US = 150;

// Map (-1.0f)-(1.0f) to 1000-2000us
static uint16_t toMicroseconds(float throttle_percent) {
    throttle_percent = constrain(throttle_percent, -1.0f, 1.0f);
    Serial.print(throttle_percent);
    return map_float(throttle_percent, -1.0f, 1.0f, ESC_MIN_US, ESC_MAX_US);
}

void motor_on(float throttle_percent, Servo &motor) {
    motor.writeMicroseconds(toMicroseconds(throttle_percent));
    Serial.println(toMicroseconds(throttle_percent));
}

// From -1.0 to 1.0
void motor_1_on(float throttle_percent) {
    motor_on(throttle_percent, motor1);
}

// From -1.0 to 1.0
void motor_2_on(float throttle_percent) {
    motor_on(throttle_percent, motor2);
}

void motor_coast(Servo &motor) {
    // In normal mode, coast is a low throttle rather than zero
    // to keep the ESC signal alive — adjust this value to suit your motor
    motor.writeMicroseconds(ESC_STOP_US + ESC_COAST_DIFF_US);
}

void motor_1_coast() {
    motor_coast(motor1);
}

void motor_2_coast() {
    motor_coast(motor2);
}

void motor_off(Servo &motor) {
    motor.writeMicroseconds(ESC_STOP_US);
}

void motor_1_off() {
    motor_off(motor1);
}

void motor_2_off() {
    motor_off(motor2);
}

void motors_off() {
    motor_1_off();
    motor_2_off();
}

void init_motors() {
    motor1.attach(MOTOR_PIN1, ESC_MIN_US, ESC_MAX_US);
    motor2.attach(MOTOR_PIN2, ESC_MIN_US, ESC_MAX_US);

    // Send stop signal immediately then hold to arm
    motors_off();
    delay(250);
}

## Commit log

2026-01-19 Add wiring diagram image to README.md
    Added image reference for wiring diagram.
2026-01-22 Update README.md
    Pin configs in `melty_config.h` should be changed.
2026-01-23 fix: arduino imports, pin assignments
    [accel_handler.cpp, led_driver.cpp, main.cpp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]
2026-01-31 Create PCB; import Teensy 4.0 symbol
    [PCB_v1.kicad_pcb, PCB_v1.kicad_sch]
2026-01-31 Finish KiCad Schematic
    [PCB_v1.kicad_sch]
2026-02-01 Import Teensy Footprints
    [PCB_v1.kicad_pcb, PCB_v1.kicad_sch]
2026-02-01 Create Footprint for DC_DC
    [PCB_v1.kicad_sch]
2026-02-01 Update DC_DC Footprint
    [PCB_v1.kicad_sch]
2026-02-01 Add and Link the Footprint of Flysky FS2A Receiver
    [PCB_v1.kicad_sch]
2026-02-01 Add LED Connector
    [PCB_v1.kicad_sch]
2026-02-01 Finish the schematics and footprints of ESC, LED and Battery
    [PCB_v1.kicad_sch]
2026-02-01 Accelerometer Footprint
    [PCB_v1.kicad_pcb, PCB_v1.kicad_sch]
2026-02-01 Fix the layer issue in ESC footprint
    [PCB_v1.kicad_pcb]
2026-02-01 Put components onto PCB
    [PCB_v1.kicad_pcb, PCB_v1.kicad_sch]
2026-02-01 Fix DC_DC Footprint
    [PCB_v1.kicad_pcb]
2026-02-01 Add Teensy-backups to .gitignore
2026-02-01 Put DC_DC back to the front layer; change the PCB layout
    [PCB_v1.kicad_pcb, PCB_v1.kicad_sch]
2026-02-01 PCB Finished
    [PCB_v1.kicad_pcb]
2026-02-01 Update PCB Appearance
    [PCB_v1.kicad_pcb]
2026-02-01 Change the Text on Silkscreen
    [PCB_v1.kicad_pcb]
2026-02-02 Separate GND (for signal) and GND_BT (for high current); make bigger holes for high current wires
    [PCB_v1.kicad_pcb, PCB_v1.kicad_sch]
2026-02-02 Fix the GND fill
    [PCB_v1.kicad_pcb]
2026-02-02 Remove the small "GND" from ESC
    [PCB_v1.kicad_pcb, PCB_v1.kicad_sch]
2026-02-03 Only Keep S Pins for ESCs
    [PCB_v1.kicad_pcb, PCB_v1.kicad_sch]
2026-02-07 gerber and drill files
    [PCB_v1-B_Cu.gbr, PCB_v1-B_Mask.gbr, PCB_v1-B_Paste.gbr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]
2026-02-07 arrange files
    [PCB_v1-NPTH.drl, PCB_v1-PTH.drl]
2026-02-07 Update PCB Layout (80mm*40mm -> 50mm*40mm)
    [PCB_v1.kicad_pcb, PCB_v1.kicad_sch]
2026-02-07 Finished PCB Layout
    [PCB_v1.kicad_pcb]
2026-02-07 Fix the Text on the PCB
    [PCB_v1.kicad_pcb]
2026-02-07 Update PCB 3D Model
2026-02-17 Increase the pad size of Teensy 4.0
    [PCB_v1.kicad_pcb]
2026-03-01 fix: motor driver to be brushless
    [motor_driver.cpp]
2026-03-01 esp32 pcb
    [ESP32_PCB.kicad_pcb, ESP32_PCB.kicad_sch, buck_converter.kicad_sch]
2026-03-02 start pcb
    [ESP32_PCB.kicad_pcb, ESP32_PCB.kicad_sch, buck_converter.kicad_sch]
2026-03-02 fix pin assignments and add en and boot jumper
    [ESP32_PCB.kicad_pcb, ESP32_PCB.kicad_sch]
2026-03-02 horizontal usb-c
    [ESP32_PCB.kicad_pcb, ESP32_PCB.kicad_sch]
2026-03-02 Increase PCB size
    [ESP32_PCB.kicad_pcb]
2026-03-02 Add LED pins, correct ESC signal pins
    [ESP32_PCB.kicad_pcb, ESP32_PCB.kicad_sch]
2026-03-15 Add two diodes for VBATT pins
    [ESP32_PCB.kicad_sch]
2026-03-15 Replace jumpers on the gyro with direct wires to avoid soldering issue
    [ESP32_PCB.kicad_sch]
2026-03-15 Add notes on schematics
    [ESP32_PCB.kicad_sch]
2026-03-15 Replace USB_D+ and USB_D- wires with labels
    [ESP32_PCB.kicad_sch]
2026-03-15 Update LED footprint
    [ESP32_PCB.kicad_sch]
2026-03-15 Remove J2 and J3's SH pins
    [ESP32_PCB.kicad_sch]
2026-03-15 Draw tracks for USB_D+ and USB_D- nets
    [ESP32_PCB.kicad_pcb]
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2026-03-16 Add tracks for buck converter and USB-C
    [ESP32_PCB.kicad_pcb]
2026-03-16 Finish EN & Boot header pins layout
    [ESP32_PCB.kicad_pcb, ESP32_PCB.kicad_sch]
2026-03-16 Add tracks for S1, S2 and LED
    [ESP32_PCB.kicad_pcb]
2026-03-16 Add tracks for gyro
    [ESP32_PCB.kicad_pcb]
2026-03-16 Place thermal pad vias
    [ESP32_PCB.kicad_pcb]
2026-03-16 Fix the size of the header pins
    [ESP32_PCB.kicad_pcb, ESP32_PCB.kicad_sch]
2026-03-16 Add labels on PCB
    [ESP32_PCB.kicad_pcb]
2026-03-16 Add screw holes and Stuffed Crust logo
    [ESP32_PCB.kicad_pcb]
2026-03-16 Import esp32 3d model
    [ESP32-S3-MINI-1U.STEP, ESP32_PCB.kicad_pcb]
2026-03-16 Adjust esp32 3D model offset
    [ESP32_PCB.kicad_pcb]
2026-03-16 Export PCB 3D model
    [ESP32_PCB.kicad_pcb, ESP32_PCB.step]
2026-03-16 Adjust USB-C 3D model offset
    [ESP32_PCB.kicad_pcb]
2026-03-16 Export 3D model
    [ESP32_PCB.step]
2026-03-16 Add 3D model for gyro
    [ESP32_PCB.kicad_pcb, ESP32_PCB.step, H3LIS331DLTR.step]
2026-03-16 Fix connection error
    [ESP32_PCB.kicad_pcb]
2026-03-16 Fix GND net isolation
    [ESP32_PCB.kicad_pcb]
2026-03-20 Change LED portion calculation
2026-03-20 Enable gyro z detection
2026-03-20 Finish motor reverse mode
    [motor_driver.cpp]
2026-03-20 Add gyro Z offset
2026-03-21 Fix low speed upside-down leftright
    [motor_low_speed.cpp]
2026-03-21 Remove "1.0f - led_on_portion"
2026-03-21 Switch Gyro to MED_RANGE
2026-03-21 Adjust gyro z offset
2026-03-21 Set motor_coast to 1500
2026-03-22 Add LED strip SPI pin labels
    [ESP32_PCB.kicad_sch]
2026-03-23 fix motor driver
2026-03-24 Add LED strip
    [ESP32_PCB.kicad_pcb, ESP32_PCB.kicad_sch, ESP32_PCB.step]
2026-03-24 Add LED to indicate the power
    [ESP32_PCB.kicad_pcb, ESP32_PCB.kicad_sch]
2026-03-24 Fix unconnected EN pin
    [ESP32_PCB.kicad_pcb]
2026-03-24 Change the direction of C12 and C13
    [ESP32_PCB.kicad_pcb]
2026-03-24 Generate gerber files
    [ESP32_PCB-B_Cu.gbl, ESP32_PCB-B_Mask.gbs, ESP32_PCB-B_Paste.gbp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]
2026-03-24 Move the text
    [ESP32_PCB-B_Cu.gbl, ESP32_PCB-B_Mask.gbs, ESP32_PCB-B_Paste.gbp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]
2026-03-30 New ESP32 led, rc, spin control rough structure
2026-03-30 Change function type in esp32_rc_handler.cpp
2026-04-01 Finish esp32 heading led (not led strip) high speed blinking control
2026-04-01 Update esp32 heading led (not led strip) calculation
2026-04-01 Import FastLED library for led strip
2026-04-01 Add led strip sector display
2026-04-02 Add a esp32 rc channel for robot facing
2026-04-02 Change the function name in esp32_rc_handler.cpp for clarification
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2026-04-02 add lcsc pn
    [ESP32_PCB.kicad_sch, buck_converter.kicad_sch]
2026-04-02 fix layout
    [ESP32_PCB.kicad_pcb]
2026-04-03 Fix LCSC and PCB
    [ESP32_PCB.kicad_pcb, ESP32_PCB.kicad_sch, buck_converter.kicad_sch]
2026-04-04 generate BOM, PNP, and update U4
    [ESP32_PCB-B_Cu.gbl, ESP32_PCB-B_Mask.gbs, ESP32_PCB-B_Paste.gbp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]
2026-04-05 Fix LED radius calculation
2026-04-06 fix U4
    [buck_converter.kicad_sch]
2026-04-07 generating bom and cpl for pcbway
    [ESP32_PCB-B_Cu.gbl, ESP32_PCB-B_Mask.gbs, ESP32_PCB-B_Paste.gbp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]
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2026-04-18 fix: throttle input, esp32 and teensy files; testing
    [led_driver.cpp, main.cpp, melty_config.h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]
2026-04-18 Fix esp32 rc callback
    [spin_control.cpp]
2026-04-18 Improve spin control: replace while loop with math
    [spin_control.cpp]
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2026-04-23 Fix high speed LED
    [led_driver.cpp, main.cpp]
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2026-04-25 Replace functions with extern variables
    [motor_low_speed.cpp]
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2026-04-25 Fix driving direction error (heading led offset still needs to be changed)
    [spin_control.cpp]
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2026-04-30 Add a second LED pin to avoid drawing too much current from one pin
    [led_driver.cpp, main.cpp, melty_config.h]
